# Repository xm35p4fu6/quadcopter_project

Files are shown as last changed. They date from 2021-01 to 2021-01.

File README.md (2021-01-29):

# 高三 Arduino 專題

> 生活科技課看到這個 Arduino 名字好像很潮就選了，也沒什麼特殊想法。
> 上網研究一下以後發現，原來是 maker 相關的東西，就像是一個小心臟，組織、控制各組件的運作來達成目的，操作邏輯簡單，使用 C-like 語言
> 最後決定做四軸機，三個傻瓜裡面會飛的那台

## 材料

- Arduino
    - 網購、學校提供
    - 作為主控制器
- 各種模塊
    - GPS / WIFI / 陀螺儀
    - 網購
- 電子變速器（電變）
    - 網購
    - 控制四顆無刷馬達
        - input: power, 4xPWM
        - output: 4x 三相交流電
- 無刷馬達x4、螺旋槳
    - 網購
    - 要注意槳規格尺寸、馬力、電變、電池的搭配
    - 正反槳至少各買兩組，一定會摔壞的，買越多越好反正很便宜
- 電池
    - 網購
    - 注意不要太重
- 木頭
    - 學校提供
- 保麗龍、電火布
    - 整體防撞要到位，測試的時候才不會馬上下課。

## 工具

- 焊接工具
    - 網購的各種零件通常需要自己焊接插頭、插座
- 木工工具
    - 四個軸使用飛機木製造
    - 線鋸機、輪鋸機、帶鋸機
        - 切出理想外觀
    - 刨木機
        - 修至精準尺寸
    - 電鑽、砂紙
        - 細節加工
- 3D 列印機
    - 四軸機本體平台、小零件可以自行列印出來用
- 雷射切割機
    - 切木料或是裝飾

## 圖文分享

### 開箱

- 用集運過來就是這樣一坨
    
- 可以多重遞迴開箱
    
- 所有店家的保護都很齊全
    
- 大部分模塊本體其實很小
    
- 淘寶來的飛行核心保護的挺好，無受損，最後收完大概只有這樣
    

### 硬體

- 反正都先串起來玩玩看
    
- 馬達，左上是起始，中上、右上開始拆封，下方是預備要把插頭焊接，鉗子配上橡皮筋，沒有固定座也能單人完成。
    
- 像這樣夾著，可以先補滿焊錫，再插電線，注意速度不要加熱太久，線跟頭都會壞掉
    
- 旁邊有個小洞，電烙鐵很好擺，先速速填銲錫，之後拿錫線換銅線就接好了
    
- 焊接完成像這樣，小時候不會對焦抱歉
    
- 接著要用熱縮套收口
    
- 加工完畢以後鎖上底盤，底盤鎖在木板上像這樣，記得先鎖穩才測試馬達
    
- 這是我用的型號
    
- 驅動馬達需要比較大電流，arduino 撐不住的，必須用電變，arduino 負責給控制訊號即可，金援夠的話，安培儘量買大不會虧，如果不是太特殊的，買這種四合一可以省空間，也比較好佈線
    
- 測試各種模組記得要先看懂規格，亂接的下場通常都是燒毀～
    
- 電池想說越大越好結果沒注意到重量，會消耗很多馬力，如果是購買已經焊好插座的形式，記得買對應的插頭回來焊在需要對接的裝置，否則會像我一樣跑去電料行找零件 ... 充電器的部分，也可以順便購買，品質會比較好可以順便監測電池狀態
    
- 主體平台我是功能導向設計，上方柱子打 Arduino 孔位，下方可以提供繞線，四邊開孔插木條，好處是摔壞能換，主體用 3d printer 印的～
    
- 一些列印的小零件
    
- 成品圖
    

### 軟韌體

> 如果對調變速率(Baud/鮑率)不熟，建議都用他人推薦的或預設即可，省去很多坑，我都用 9600，有時候某些模塊會需要設定，用 `SoftwareSerial` 設定對應腳位的 baud

- 電子變速器
    - 通常用 電變、esc 測試之類的關鍵字，稍微找一下就可以找到測試用的程式碼了
    - 自己修改一下用來測試是否正常，也可以用來參考如何控制電變
    
- GPS
    - 顯示模塊印出資訊，GPS 買太爛或供電不足會很秀抖，要注意是否是供電不足，因為他還是能運作，只是很坑，Arduino 應該是無法負荷他需要的電力，需要自己從電池拉電。
    
- 陀螺儀
    - 陀螺儀部分建議買 arduino 出的模塊，不要自己買散裝的便宜貨，因為通訊指令有差，arduino 內建已經寫好一份 ADXL345 的，可以直接用比較方便。
    - 測好之後跟馬達一起實作 PID 演算法，測試時要確認運作是沒有延遲的，也就是一傾斜馬上對應馬達加速。
    - [PID 詳細解說](http://www.inpharmix.com/jps/PID_Controller_For_Lego_Mindstorms_Robots.html)
- wifi
    - 這邊也是建議買官方的模塊，但是官方模塊真的有點大、貴，買野生模塊記得要挑實作好 TCP/UDP、開基地台、連接基地台函式庫的。
    - 這邊也是要注意供電，不夠的話跟 GPS 一樣，會有問題且繼續運作，很難抓錯，供電一定要夠，從電池拉電比較穩。
    - 測試一定要時刻確定保持連線，失聯馬上停馬達（墜機），確認好才上螺旋槳。
    - 上網找範例的關鍵字：socket server client 

## 結語

因為我最終也沒有做出能穩定起飛降落的版本，每次測試都是墜機，加上各種硬體的通訊方式有蠻大差別，所以程式碼還是上網找範例參考較好，我附上的大多是測試程式碼，準備學測就沒繼續胡搞了，僅分享一些心得希望做類似項目的人少踩點坑！

## 網購紀錄

> 很多品項應該失聯了，主要是記錄，以及有一些注意事項

```
老師要的賣家網址:(PS:台灣網拍在服務、價位、與賣家直接對談方面，完全沒競爭力，故選擇淘寶)

集運：
http://shop59449044.taobao.com/shop/view_shop.htm?spm=a1z09.2.9.4.4aVaQz&user_number_id=273972448&v=1
~~~公主集運
集運，服務態度極佳(配台灣黑貓)

ａｒｄｕｉｎｏ：
http://item.taobao.com/item.htm?spm=a1z09.2.9.32.4aVaQz&id=37833297988&_u=q22s4eihd043
~~~Arduino MEGA2560 R3 ??板（2012新版本,ATMEGA16U2,官方版本）
服務態度佳，出貨速度偏慢(需催)

鋰電池＋充電：(需自行焊接)
http://item.taobao.com/item.htm?spm=a1z09.2.9.54.4aVaQz&id=37033373520&_u=q22s4eih80b9
~~~5200MAH/30C T插?技???: ?子11.1V/3S??池
~~~IMAXB6（工厂直?）技???: 套餐一
原廠直銷，服務佳

馬達＋槳：(需自行焊接)
http://item.taobao.com/item.htm?spm=a1z09.2.9.76.4aVaQz&id=21112544886&_u=q22s4eih44b2
~~~白色?机种?: 1??（1正+1反）
~~~?配+香蕉?+??管技???: 2212/1000KV
服務態度佳，ㄠ贈品成功(槳+1對)

陀螺儀：
http://item.taobao.com/item.htm?spm=a1z09.2.9.104.4aVaQz&id=19882412955&_u=q22s4eih953c
新款 ADXL345 IIC /SPI ?字式 ?角?感器 加速度模?
價格極便宜，不建議購買(無技術支援、與arduino開發的ADXL345模組，同晶片不同指令、偏遠地區重慶，貨運較久)

電變（ＥＳＣ）：(需自行焊接)
http://item.taobao.com/item.htm?spm=a1z09.2.9.122.4aVaQz&id=15836442787&_u=q22s4eiha7dc
好盈天行者四合一??技???: 20A
(正版帶雷標)原廠已停產，不建議購買，改選25A較佳

ＷＩＦＩ模組：
http://item.taobao.com/item.htm?spm=a1z09.2.9.138.4aVaQz&id=40901823151&_u=q22s4eih2316
OCROBOT SEED WIFI模? ESP8266 陶瓷天? at指令控制 arduino
與老師的wifi同晶片不同公司，客服為技術人員服務佳，函式庫bug多、使用不同AT指令，不建議購買

ＧＰＳ模組：
http://item.taobao.com/item.htm?spm=a1z09.2.9.154.4aVaQz&id=38609168111&_u=q22s4eih2378
GY-NEO6MV2 ?控GPS模? ?EEPROM MWC APM2.5?控 NEO-6M
ㄠ到贈品(排針)
```

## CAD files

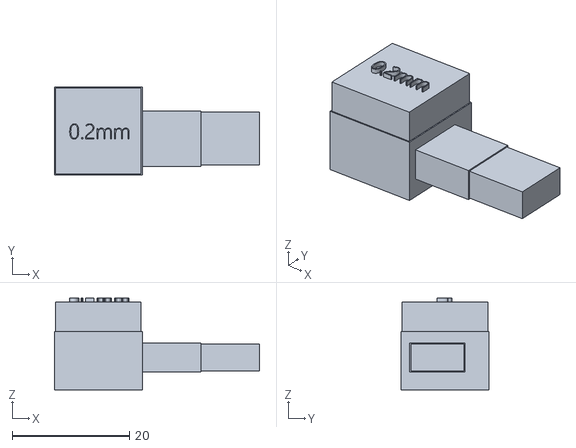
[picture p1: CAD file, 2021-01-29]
code/sketch_up/測試.stl
35.0 x 15.0 x 15.7

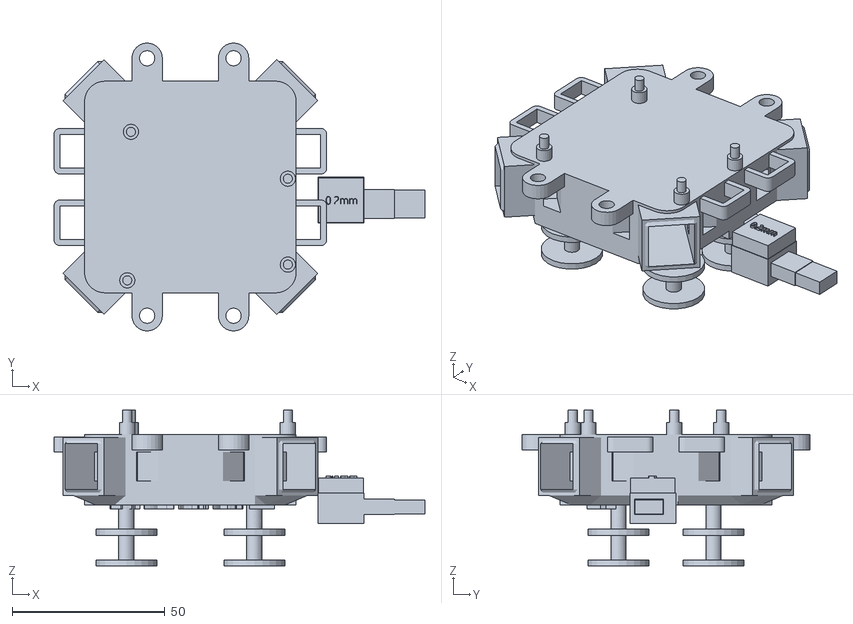
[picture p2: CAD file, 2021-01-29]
code/sketch_up/31304.stl
121.5 x 94.3 x 51.0

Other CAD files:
code/adxl345/ExampleCode_iMEMs_ADXL345/4-wire/MAIN.OBJ
code/adxl345/ExampleCode_iMEMs_ADXL345/4-wire/CONFIG.OBJ
code/adxl345/ExampleCode_iMEMs_ADXL345/4-wire/startup.OBJ
code/adxl345/ExampleCode_iMEMs_ADXL345/4-wire/SPI.OBJ
code/sketch_up/2013用/四軸機中心插銷(未校正)2013.skp
code/sketch_up/2013用/四軸機中心結構 (1)2013.skp
code/sketch_up/2013用/第一節手臂2013.skp
code/sketch_up/2013用/第三節手臂2013.skp
code/sketch_up/2013用/第二節手臂2013.skp
code/sketch_up/四軸機中心插銷(未校正).skp
code/sketch_up/四軸機中心結構.skp
code/sketch_up/插銷(新).skp
code/sketch_up/測試.skp
code/sketch_up/第一節手臂.skp
code/sketch_up/第三節手臂.skp
code/sketch_up/第二節手臂.skp

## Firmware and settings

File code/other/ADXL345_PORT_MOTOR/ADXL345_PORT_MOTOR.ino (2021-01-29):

/*
1.
MUX:0 單鏈 / 1 雙鏈 (int)

2.
UDP/TCP(String) ， "IP位址"(String)， 端口(int)
*/
#include<Servo.h>
#include<Wire.h>
#include<ADXL345.h>
unsigned long time_setup;
////////////MOTOR///////////////
int motor_pin[4] = {2,3,4,5};
Servo motor[4];
int throttle_in=0;
///////////ADXL345///////////////
const float alpha = 0.5;

double fXg = 0;
double fYg = 0;
double fZg = 0;

ADXL345 acc;

void setup(){
  pinMode(13,OUTPUT);
  acc.begin();
  Serial.begin(9600);
  Serial1.begin(9600);
  while(!Serial1);
  Serial1.println("AT+JoinAP?");
  String data;
  while(1){
    if(Serial1.available()>0){
      char a = Serial1.read();
      data+=a;
    }
    if(data.indexOf("done")!=-1 || data.indexOf("ERROR")!=-1)break;
  }
  //Data processing
  char head[4] = {0x0D,0x0A};
  char tail[7] = {0x0D,0x0A,0x0D,0x0A};
  data.replace("AT+JoinAP?","");
  data.replace("+JoinAP:","wifi : ");
  data.replace("done","");
  data.replace(head,"");
  data.replace(tail,"");
  Serial.println(data);
  Serial.println("set MUX : 0 / 1 ");
  while(Serial1.available()>0){
    Serial1.read();
    delay(1);
  }
  while(1){
    if(Serial.available()>0){
      char a = Serial.read();
      Serial1.println("AT+MUX="+(String)a);
      Serial.println("sent : AT+MUX="+(String)a);
    }
    if(Serial1.available()>0){
      char a = Serial1.read();
      if (a == 'e')break;      //done
    }
  }
  Serial.print("U/T : ");
  String data_U_T;
  while(1){
    if(Serial.available()>0){
      char a = Serial.read();
      switch(a){
      case 'U':
        data_U_T="UDP";
        break;
      case 'T':
        data_U_T="TCP";
        break;
      default:
        Serial.println("UorT");
      }
      break;
    }
  }
  Serial.println(data_U_T);
  Serial.print("IP : ");
  String data_IP;
  while(1){
    if(Serial.available()>0){
      char a = Serial.read();
      data_IP+=(String)a;
      delay(1);
      if(Serial.available()==0)break;
    }
  }
  Serial.println(data_IP);
  Serial.print("port : ");
  String data_port;
  while(1){
    if(Serial.available()>0){
      char a = Serial.read();
      data_port+=a;
      delay(1);
      if(Serial.available()==0)break;
    }
  }
  Serial.println(data_port);
  Serial.println("SENT :AT+NewSTA=\"" + data_U_T + "\",\"" + data_IP + 
                 "\"," + data_port );
  Serial1.println("AT+NewSTA=\"" + data_U_T + "\",\"" + data_IP + 
                 "\"," + data_port );
  while(1){
    delay(1);
    //Serial.print(".");          //
    if(Serial1.available()>0){
      char a = Serial1.read();
      Serial.print(a);              //
      delay(1);
      if(Serial1.available()==0){
        Serial1.println("AT+UpDate=10");
        while(1){
          if(Serial1.available()>0){
            Serial1.println("0123456789");
            while(1){
              if(Serial1.available()>0){
                //Serial.print(",");
                char b = Serial1.read();
                Serial.print(b);
                if(b=='K')break;            //SEND OK
              }
            }
            break;
          }
        }
        Serial.println("Done and sent 'test' to the port. ");
        break;
      }
    }
  }
  while(Serial.available()>0){
    Serial.read();
    delay(1000);
  }
  while(Serial1.available()>0){
    Serial1.read();
    delay(1000);
  }
  Serial.println("WIFI OK.");
  ////////////////////////
  for(int i = 0 ; i < 4 ; i++ )
    motor[i].attach(motor_pin[i]);
  Serial.println("START");
  time_setup=millis();
  
}
//////////////////
//////////////////
//////////////////
//////////////////
//////////////////
void loop(){
  /*冒號前 往後讀*/
  if(Serial1.available()>0){
    if((char)Serial1.read()=='+'){    //確認接收
      String get;
      while(1){
        int a=Serial1.read();
        if(a==101)break;
        if(a>=33 && a<=127)
        get+=(char)a;
      }
      //提出
      //Serial.println("\n\n");
      //Serial.println(get);
      int len=get[4]-48;  //before ':'，ascii char to int
      throttle_in=0;
      for(int i = 6 ; i<(6+len) ; i++){
        throttle_in*=10;
        //Serial.print(throttle_in);
        throttle_in+=int(get[i]-48);
        //Serial.println(throttle_in);
      }
      Serial.println(throttle_in);
      /*~get~*/
    }
    for(int i = 0 ; i<4 ; i++ )
    motor[i].write(throttle_in);
  }
  ////////////ADXL345return//////////////
  unsigned long time_here=millis()-time_setup;
  if(time_here%500==0){
    double pitch , roll , Xg , Yg , Zg;
    acc.read(&Xg,&Yg,&Zg);
    fXg = Xg * alpha + (fXg * (1.0 - alpha));
    fYg = Yg * alpha + (fYg * (1.0 - alpha));
    fZg = Zg * alpha + (fZg * (1.0 - alpha));
    roll  = (atan2(-fYg, fZg)*180.0)/M_PI;
    pitch = (atan2(fXg, sqrt(fYg*fYg + fZg*fZg))*180.0)/M_PI;
    int Ipitch=int(pitch+0.5);
    int Iroll=int(roll+0.5);
    String p= Ipitch +(String)" " + Iroll +(String)" "+ (String)Zg;
    Serial1.print("AT+UpDate=");
    Serial1.println(p.length());
    while(1){
          if(Serial1.available()>0){
            Serial1.println(p);
            while(1){
              if(Serial1.available()>0){
                //Serial.print(",");
                char b = Serial1.read();
                if(b=='K'){
                  Serial1.read();
                  Serial1.read();
                  break;            //SEND OK
                }
              }
            }
            break;
          }
        }
    }
}

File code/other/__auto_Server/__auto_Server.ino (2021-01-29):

#include<Servo.h>
#include<Wire.h>
#include<ADXL345.h>

int motor_pin[4] = {2,3,4,5};
Servo motor[4];
int Speed[4] = {0,0,0,0};

double standardAcceData[3] = {0,0,0.89};  //sensors data ADXL
double currentAcceData[3] ;
ADXL345 adxl345;

double errorX , errorY , tFix[4] = {0,0,0,0} ;  //PID
double Kp = 35 , Ki = 1.5 , Kd = 10 ; 

void setup(){
  Serial.begin(9600);
  Serial1.begin(9600);
  while(!Serial1){Serial.print("WIFI");}
  Serial1.println("AT+MUX=1");
  Serial1.println("AT+Server=1,31304");
  
///////////////////////////
  for(int i = 0 ; i < 4 ; i++ )
    motor[i].attach(motor_pin[i]);
///////////////////////////
  adxl345.powerOn();
///////////////////////////
  while(Serial1.available()>0){
    Serial1.read();
    delay(5);
  }
  for(int i=0;i<4;i++) motor[i].write(20);
  Serial.println("u can fly...");
}
void loop(){
  while(!Serial1){
    motor[0].write(0);
    motor[1].write(0);
    motor[2].write(0);
    motor[3].write(0);
  }
  get_inSpeed();
  while(Speed[0] == 0 && Speed[1] == 0 && Speed[2] == 0 && Speed[3] == 0){
    for(int j=0;j<4;j++){
      motor[j].write(25);
    }
    get_inSpeed();
  }
  while(Speed[0] == 111 && Speed[1] ==222 && Speed[2] ==333 && Speed[3]==444){
    for(int j=0;j<4;j++){
      motor[j].write(20);
    }
    get_inSpeed();
  }
  get_AcceData();
  calculatePID();
  send_motor();
}


void get_inSpeed(){
  if(Serial1.available()>0){
    if((char)Serial1.read()=='+'){
      String get;
      while(1){
        int a=Serial1.read();
        if(a>=33 && a<=127)get+=(char)a;
        if(a==101)break;
      }
      for(int i = 0 ; i < 4; i++ ){
        Speed[i] = 0;
        Speed[i] += int( get[9 + 3*i ] - 48 );
        Speed[i] *= 10;
        Speed[i] += int( get[10 + 3*i ] - 48 );
        Speed[i] *=10;
        Speed[i] += int( get[11 + 3*i ] - 48 );
      }
    }
  }
}

void get_AcceData(){
  adxl345.get_Gxyz(currentAcceData);
}

void calculatePID(){
  for(int i=0;i<4;i++){
    tFix[i]=0;
  }
  // caculata error
  errorX = currentAcceData[0] - standardAcceData[0];
  errorY = currentAcceData[1] - standardAcceData[1];
  
  //P (X axis)
  tFix[0] -= Kp * errorX;
  tFix[2] += Kp * errorX;
  //P (Y axis)
  tFix[1] -= Kp * errorY;
  tFix[3] += Kp * errorY;
}

void send_motor(){
  for(int i=0;i<4;i++){
    int fix = (int)tFix[i];
    int f = Speed[i] + fix ;
    motor[i].write(f);
  }
}
